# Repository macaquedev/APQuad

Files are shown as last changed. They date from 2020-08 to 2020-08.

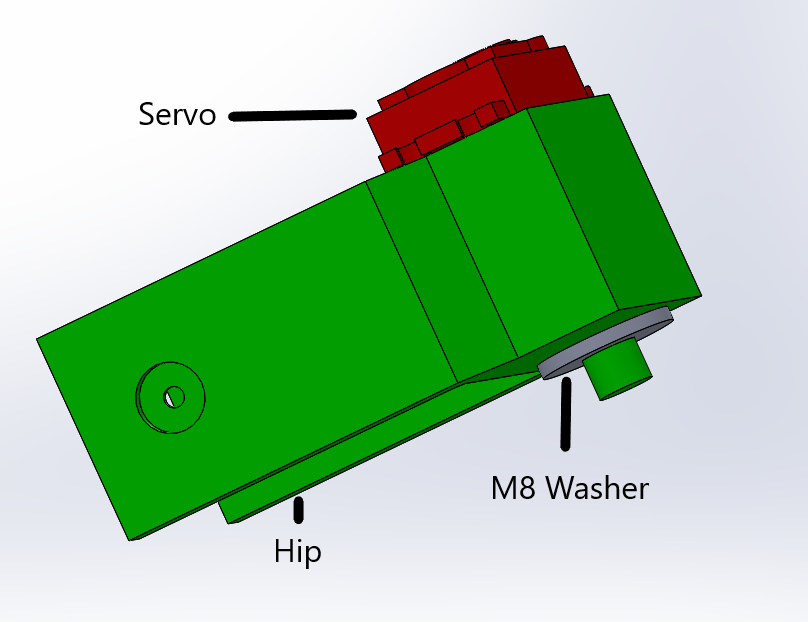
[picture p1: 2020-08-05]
Diymore MG996R/Building Instructions/Photos/Hip Assembly.png

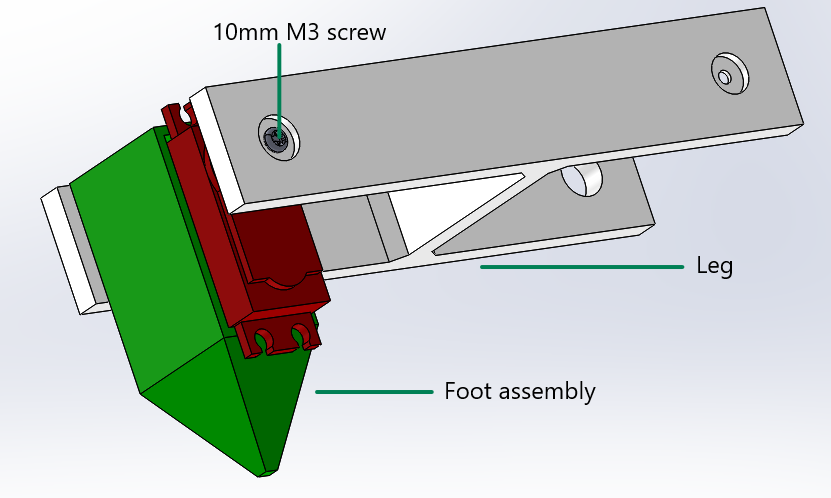
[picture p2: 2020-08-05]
Diymore MG996R/Building Instructions/Photos/Connecting Foot assembly to Leg.png

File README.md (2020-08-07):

An Arduino Quadruped designed to be as straightforward as possible to use and make.

I have posted all code, all STL's and all building instructions on this Github repository.

Please share this repository if you have found this helpful.

Please post a comment or email me at macaquedev@gmail.com if you need help or feel something is wrong.

DISCLAIMER - I hold no responsibility for any damage caused. This is a project that has gone through hours of rigorous testing, which means there is very little risk of something being wrong in the project, but it is very easy to connect something incorrectly. Please double check ALL electronics before switching on your APQuad for the first time.

To start, please clone this repository and then choose a servo out of the ones I have mentioned above. Then please go into the folder with the same name as the servo you are using for your APQuad and read the relevant README files.

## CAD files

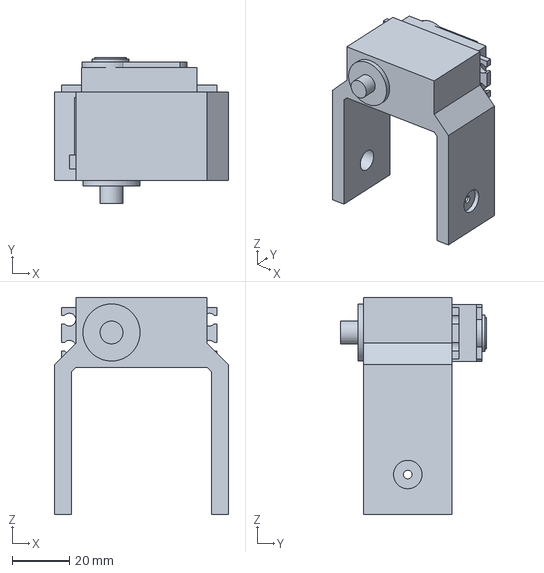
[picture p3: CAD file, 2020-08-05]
Diymore MG996R/Building Instructions/3D Models/Mirrored Hip Assembly.3MF
61.0 x 51.0 x 76.0 mm

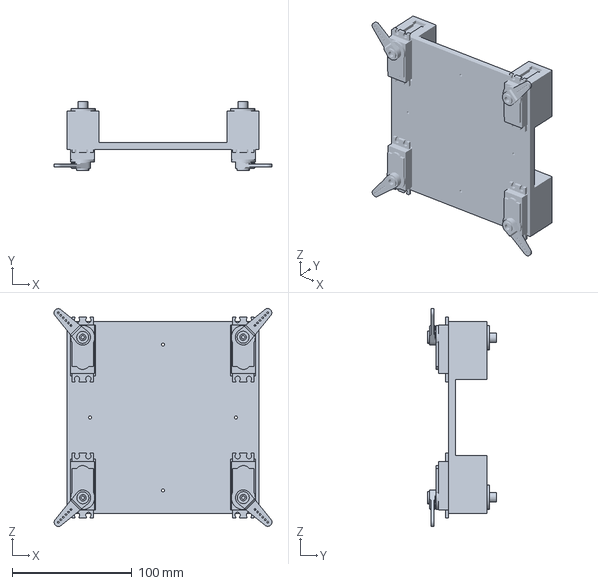
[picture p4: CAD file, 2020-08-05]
Diymore MG996R/Building Instructions/3D Models/Base Plate Assembly.3MF
181.9 x 57.5 x 181.9 mm

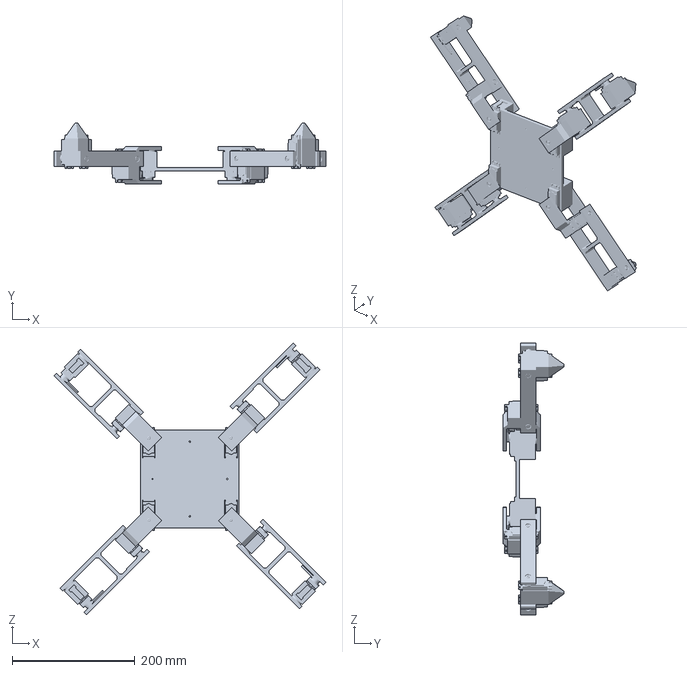
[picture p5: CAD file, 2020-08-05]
Diymore MG996R/Building Instructions/3D Models/Full APQuad Assembly.3MF
442.4 x 99.5 x 441.7 mm

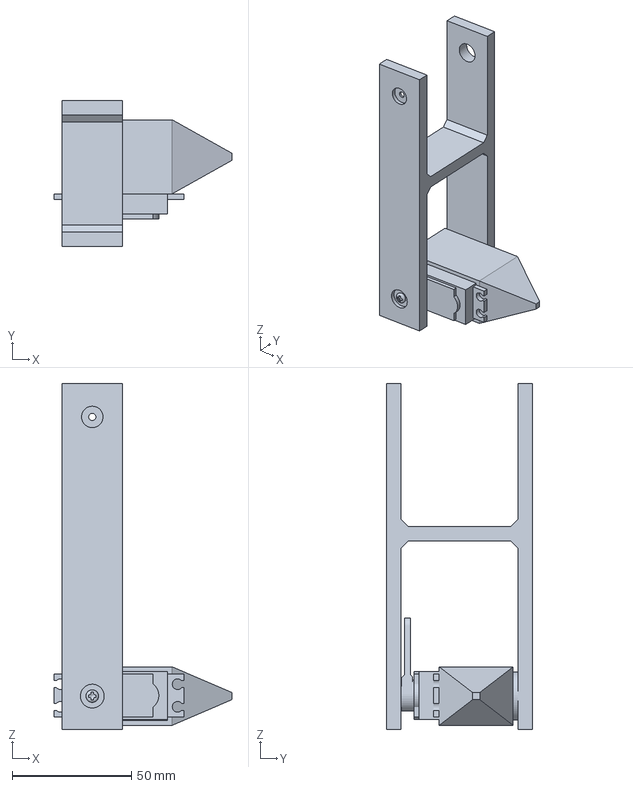
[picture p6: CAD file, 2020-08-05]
Diymore MG996R/Building Instructions/3D Models/Connecting Foot assembly to Leg.3MF
74.5 x 61.0 x 145.0 mm

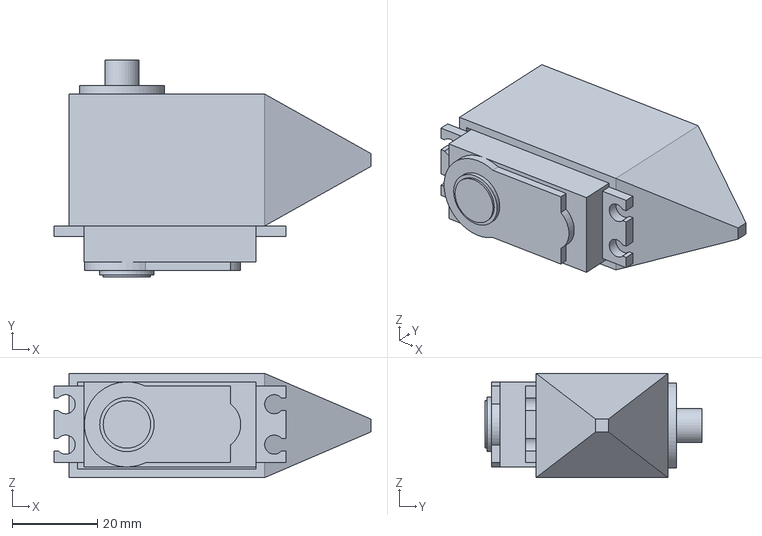
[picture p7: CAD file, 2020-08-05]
Diymore MG996R/Building Instructions/3D Models/Foot assembly.3MF
74.5 x 51.0 x 24.5 mm

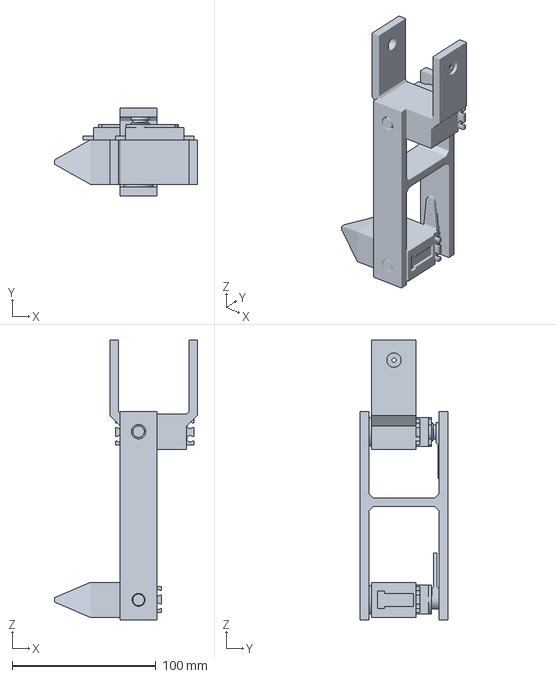
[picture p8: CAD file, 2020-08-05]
Diymore MG996R/Building Instructions/3D Models/Leg with Mirrored Hip assembly.3MF
99.5 x 61.0 x 194.8 mm

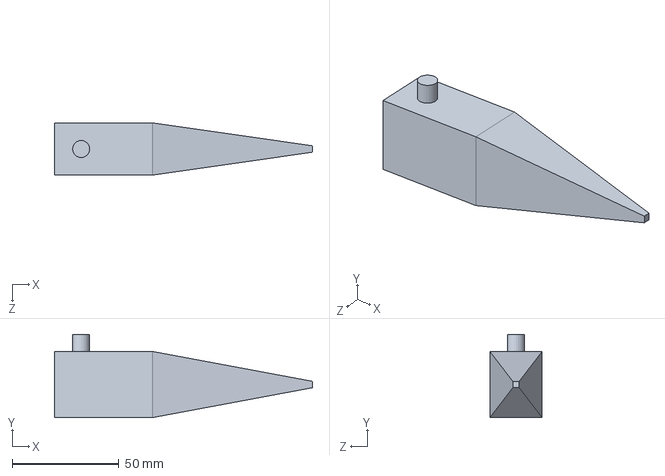
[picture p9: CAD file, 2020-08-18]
Diymore MG996R/SLDPRT (to modify files in Solidworks)/Foot.SLDPRT
121.0 x 39.0 x 24.5 mm

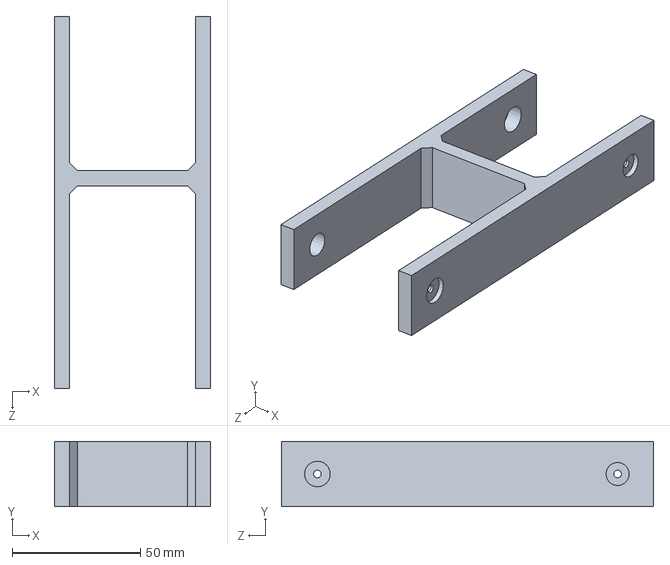
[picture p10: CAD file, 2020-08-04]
Diymore MG996R/SLDPRT (to modify files in Solidworks)/Leg.SLDPRT
61.0 x 25.5 x 145.0 mm

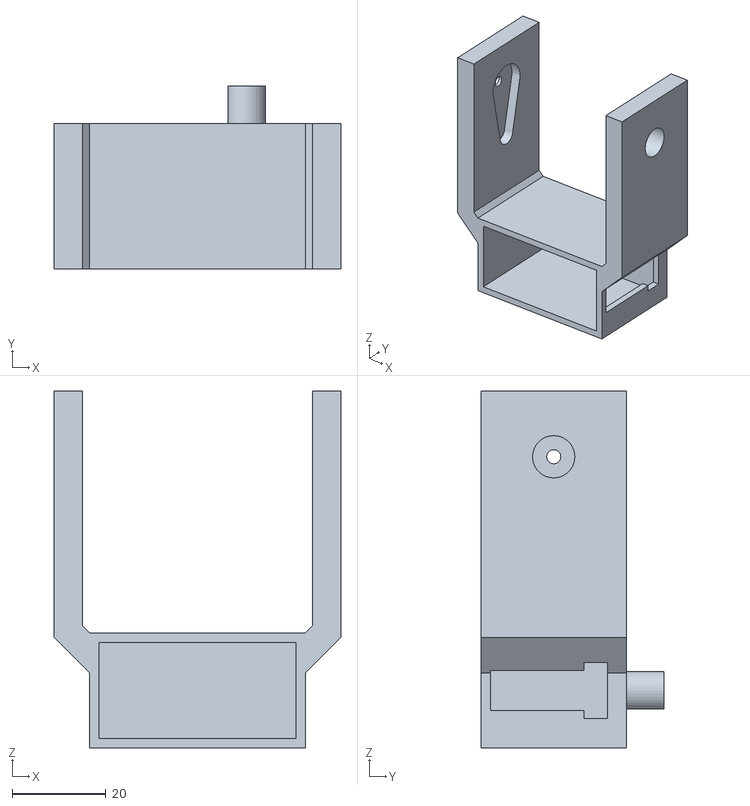
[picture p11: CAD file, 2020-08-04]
Diymore MG996R/To 3D print/Hip.STL
61.0 x 39.0 x 76.0

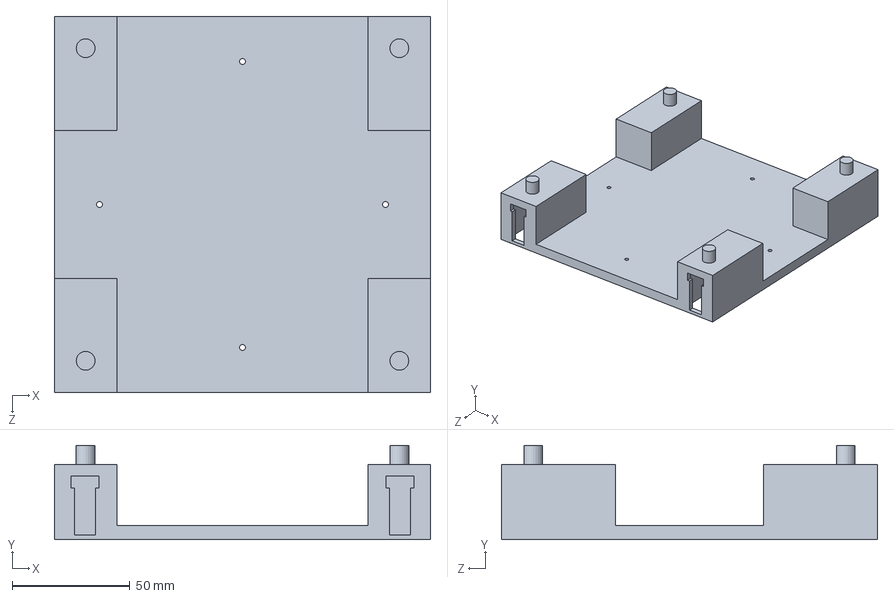
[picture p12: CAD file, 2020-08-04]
Diymore MG996R/SLDPRT (to modify files in Solidworks)/Base Plate.SLDPRT
160.0 x 40.0 x 160.0 mm

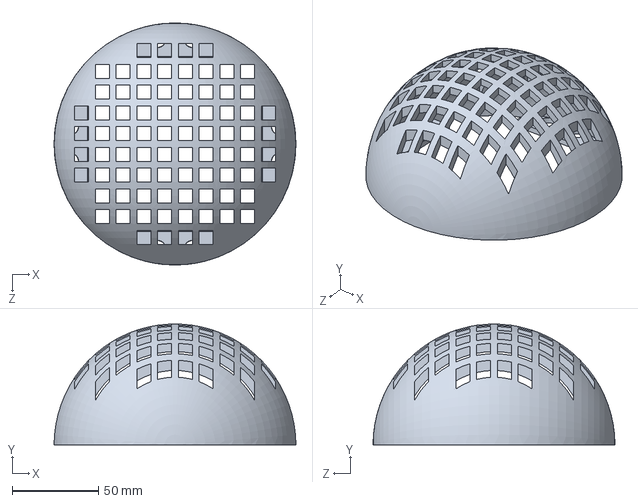
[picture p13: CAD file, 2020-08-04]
Diymore MG996R/SLDPRT (to modify files in Solidworks)/Dome.SLDPRT
140.0 x 69.9 x 140.0 mm

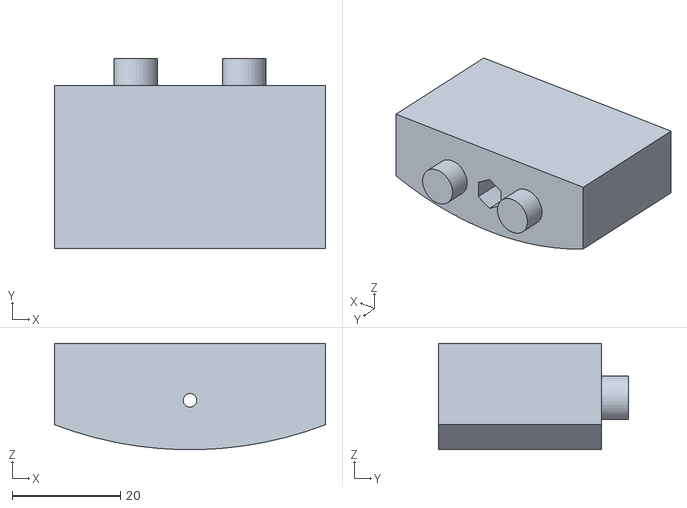
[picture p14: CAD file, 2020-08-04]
Diymore MG996R/To 3D print/Mount for dome.STL
50.0 x 35.0 x 19.6

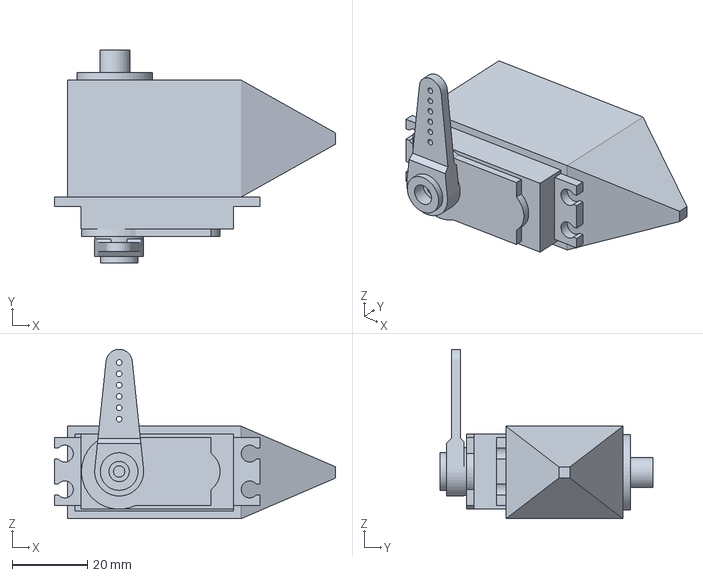
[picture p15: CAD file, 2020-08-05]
Diymore MG996R/Building Instructions/3D Models/Adding attachment to Foot.3MF
74.5 x 56.5 x 44.9 mm

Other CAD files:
Diymore MG996R/Building Instructions/3D Models/Hip Assembly.3MF
Diymore MG996R/Building Instructions/3D Models/Leg with Hip assembly.3MF
Diymore MG996R/To 3D print/Foot.STL
Diymore MG996R/To 3D print/Leg.STL
Diymore MG996R/SLDPRT (to modify files in Solidworks)/Hip.SLDPRT
Diymore MG996R/Building Instructions/3D Models/Adding attachment to Hip.3MF
Diymore MG996R/Building Instructions/3D Models/Adding attachment to Mirrored Hip.3MF
Diymore MG996R/SLDPRT (to modify files in Solidworks)/Leg with tabs for warping prevention.SLDPRT
Diymore MG996R/SLDPRT (to modify files in Solidworks)/Mirrored Hip.SLDPRT
Diymore MG996R/SLDPRT (to modify files in Solidworks)/Mount for dome.SLDPRT
Diymore MG996R/To 3D print/Base Plate.STL
Diymore MG996R/To 3D print/Dome.STL
Diymore MG996R/To 3D print/Leg with tabs for warping prevention.STL
Diymore MG996R/To 3D print/Mirrored Hip.STL

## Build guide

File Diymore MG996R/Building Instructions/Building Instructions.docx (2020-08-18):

Building Instructions for APQuad 3DoF models

Alex Pylypenko (macaquedev)

NOTE:

These will work for ANY model of APQuad with ANY servo (other than 2DOF versions). The parts may look slightly different depending on which model you have, but please rest assured that the assembly WILL be correct no matter which servo is used. However, the Electronics part is slightly different for 9g servos.

DISCLAIMERS:

I hold NO responsibility whatsoever for any damage done or injuries caused by carelessness or incorrect assembly.

This is presented ‘as is’ with ABSOLUTELY NO WARRANTY.

Mechanical Assembly:

3D printed parts required (can be commercially printed):

1x Base Plate.stl

4x Foot.stl

4x Leg.stl

2x Hip.stl

2x Mirrored Hip.stl

These files are located in the ‘To 3D print folder’

Optional:

1x Dome.stl

3x Mount for dome.stl

Mechanical parts required:

12x Servo motors (please use the servo you chose the designs for)

12x M8 washers

15x 10mm M3 screws (12 if not using dome)

Tools required:

Screwdriver (type dependent on the screws you are using)

3D printer

Prusaslicer or equivalent slicer (unless printed commercially)

Note before assembly: if any of this is unclear, please go into:

Building Instructions/3D Models and then see 3D models.

Instructions:

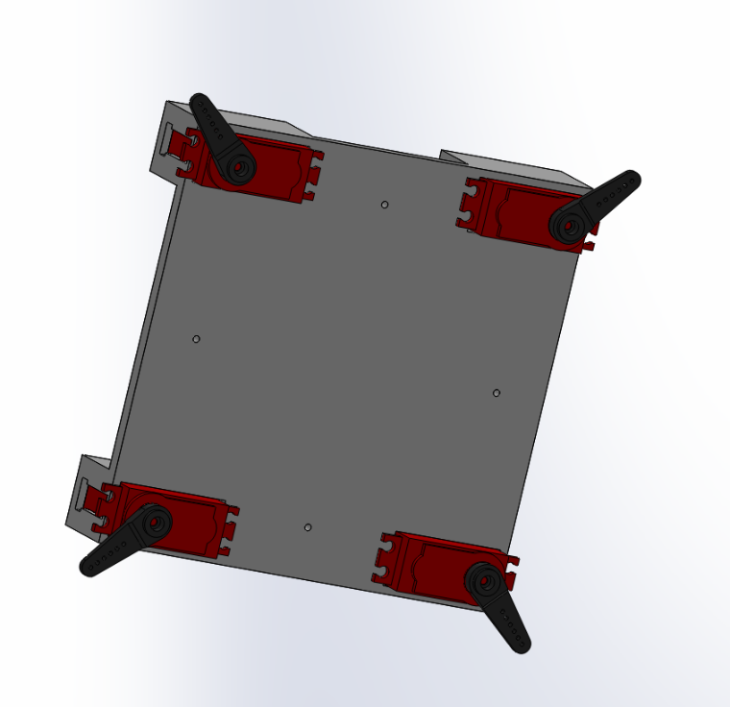
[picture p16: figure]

1. Assemble the base plate as per the images below

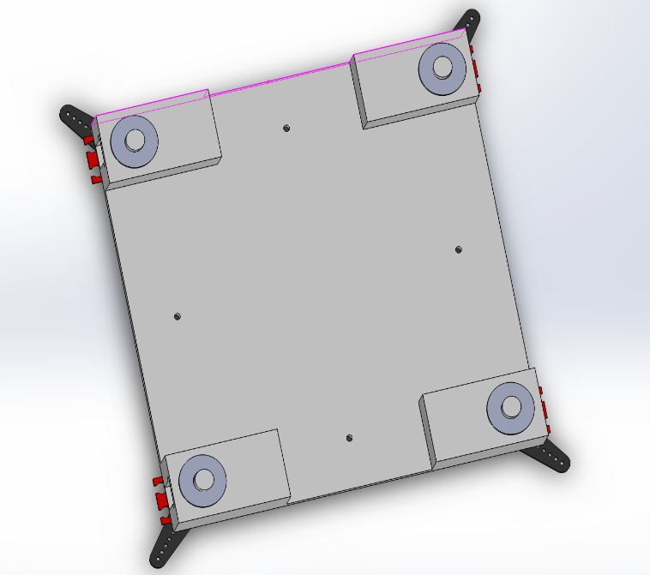
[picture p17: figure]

This step requires 4 servos, 4 washers, 4 attachments and a Base Plate.

This step is rather self-explanatory. However, before attaching the servo attachments completely, please attach them so that the angles shown on the image are the midpoints of the servo’s full turn angle so that the Arduino command moveServo(blh, 90); moves the back left hip to the position illustrated in the diagram above (top left).

2. Assemble all the feet as per the image below.

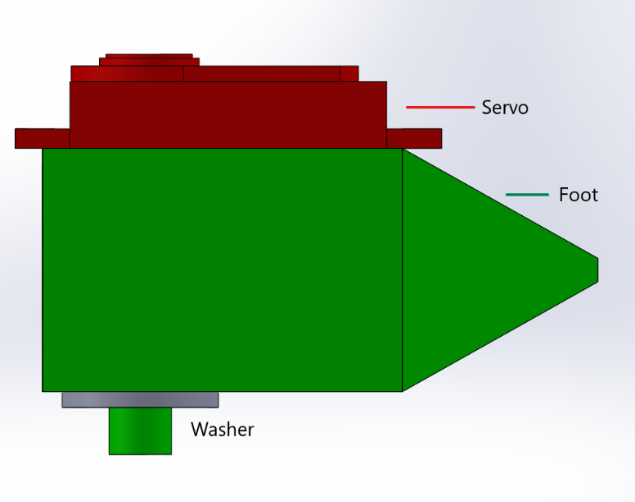
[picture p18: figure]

3. Add the attachments onto the servos. Please follow the instructions in step 1 as to what to do with the attachments (regarding midpoints etc.), however, please make 2 feet as in the diagram below and 2 feet with the attachment 180 degrees from where it is in the diagram below. Please keep the ones that are as per the diagram away from the mirrored ones and please remember which ones aren’t mirrored and which ones are.

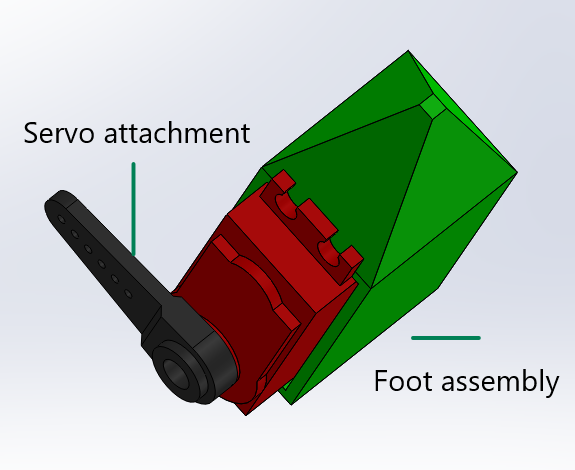
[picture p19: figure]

4. Add the legs to the foot assemblies. The mirrored ones and the non-mirrored ones will look slightly different, but that is totally correct.

Please make sure that the servo attachment goes into its designated hole. Please put it into the LONGER end of the leg.


5. Assemble the two hips and the two mirrored hips as shown in the diagrams below. Again, the angles shown in the diagram should be the midpoint of the servo’s angle of rotation.

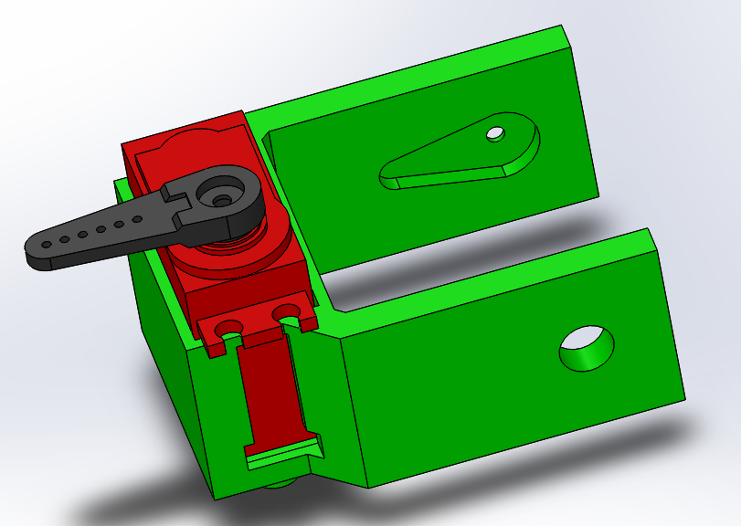
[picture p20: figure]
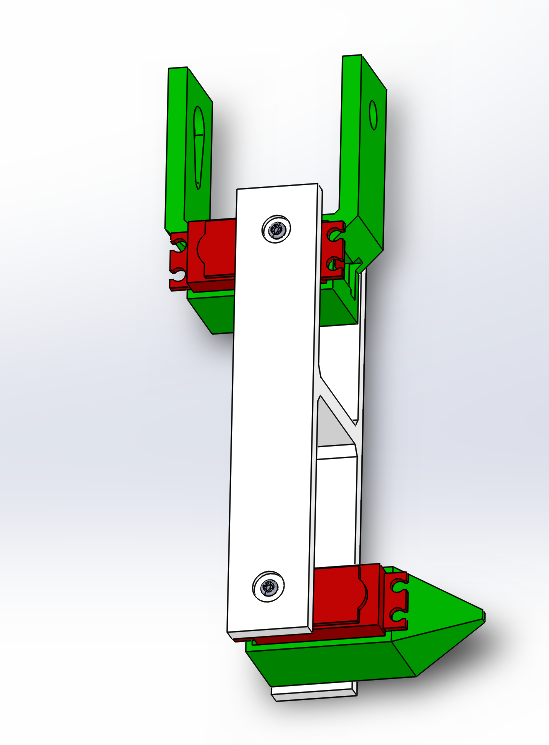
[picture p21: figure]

6. Insert the hips into the non-mirrored legs and the mirrored hips into the mirrored legs into the other ends of the leg. Please see diagram on how this should look. If it doesn’t look right, you have probably used a non-mirrored leg with a mirrored hip.
7. Before finishing the mechanical assembly of the APQuad, make sure that you have the following:
  a. 2 Legs with normal Hips
  b. 2 Legs with Mirrored Hips
  c. A fully assembled Base Plate as shown in Step 1

If not, please reread the manual. As an ABSOLUTE LAST RESORT, please email macaquedev@gmail.com with DETAILED information about your issue. Please include photos if possible. I will be very happy to answer any questions but please consider the fact that I am very busy. I will try to respond to any emails within 24 hours but if this isn’t the case, please do not spam me with emails.

8. If you have completed the checklist in question 7, please finish assembling your APQuad as shown below. The front of the APQuad is on between the top 2 legs on the image.

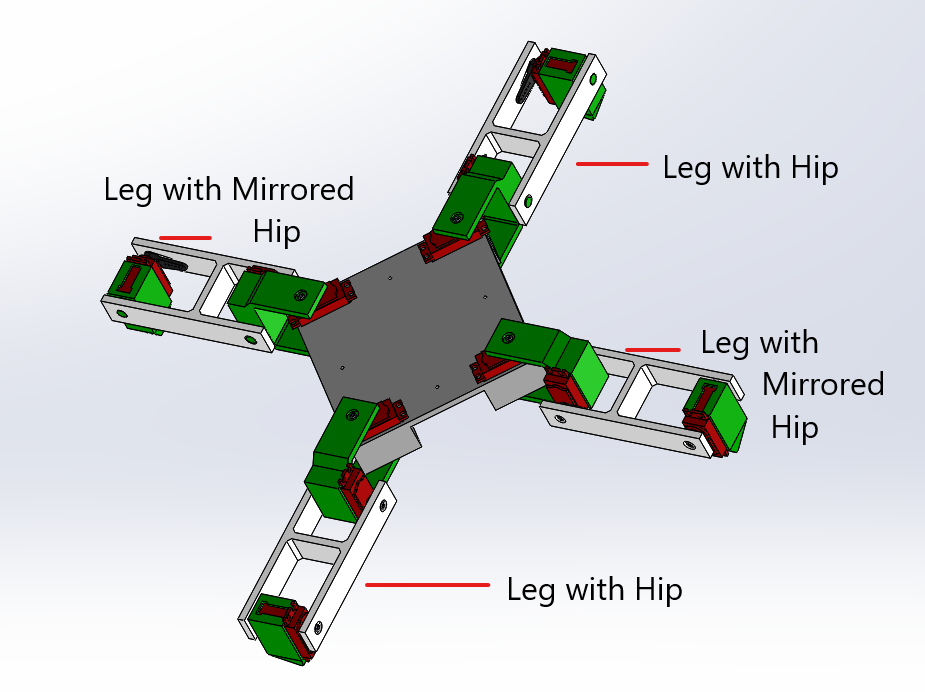
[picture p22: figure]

This is the end of the mechanical assembly. Please carry on with the electronic assembly.

Electronics Assembly (for non-9g servos):

Parts required:

Arduino Nano

PCA9685 servo multiplexer

A 3s LiPo battery

A load of jumper wires of all types

Thick wire (for high amperages)

Thinner wire (for low amperages)

R1966ablkblkff switch

10A 150W DC DC stepdown converter

LM2596S stepdown converter

A piece of PCB

Tools required:

Glue Gun

Soldering iron

Multimeter

NOTE: THIS PART IS QUITE FIDDLY AND IT IS VERY EASY TO DO SOMETHING WRONG. LITHIUM BATTERIES ARE VERY FLAMMABLE AND CAN CAUSE A MAJOR FIRE IF NOT CONNECTED PROPERLY.

Connect both converters in parallel to the battery through the switch. Check that output voltage of both converters is exactly 5V when supplying battery’s output voltage. Connect the Arduino to the 2A converter via VIN and the servo board to the 10A converter via the terminal block.

Solder 3 rows of roughly 10 female pin headers. Connect them together underneath using a soldering iron. Connect 1 row to Ground, 1 row to 3.3v and 1 row to 5v

Electronic Assembly for 9g servos:

Parts required:

Arduino Nano (use a clone to save money)

PCA9685 servo multiplexer

A 2s LiPo battery (I salvaged one from an old laptop but any will do)

A load of jumper wires of all types

Thick wire (for high amperages)

Thinner wire (for low amperages)

R1966ablkblkff switch

2x LM2596S stepdown converter

A piece of PCB

Tools required:

Glue Gun

Soldering iron

Multimeter

NOTE: THIS PART IS QUITE FIDDLY AND IT IS VERY EASY TO DO SOMETHING WRONG. LITHIUM BATTERIES ARE VERY FLAMMABLE AND CAN CAUSE A MAJOR FIRE IF NOT CONNECTED PROPERLY.

Connect both converters in parallel to the battery through the switch. Check that output voltage of both converters is exactly 5v when supplying battery’s output voltage. Connect the two converters’ outputs together. Connect both the Arduino (via VIN) and the servo board (via terminal holes) to the converters’ outputs.

Solder 3 rows of roughly 10 female pin headers. Connect them together underneath using a soldering iron. Connect 1 row to Ground, 1 row to 3.3v and 1 row to 5v

Electronic Assembly continued for ALL servos:

Connect the servo board to the Arduino:

Servo Board | Arduino (or power rail if applicable)
GND | GND
VCC | 3.3v
SCL | A5
SDA | A4

Connect the servos to the Servo Board:

B=back, F=front, L=left, R=right, A=ankle, K=knee, H=hip

Servo | Servo
FLA | 0
FLK | 1
FLH | 2
FRA | 3
FRK | 4
FRH | 5
BLA | 6
BLK | 7
BLH | 8
BRA | 9
BRK | 10
BRH | 11

This is it for the Electronic Assembly.

NOTE: It is recommended for the Arduino Nano’s USB to be facing the back of the robot and to be easy to access from outside.

Adding the Dome (optional):

This step is extremely self-explanatory. Note – the part missing a Mount should be where the Arduino Nano’s USB port is facing. This is done so that the USB port is easily accessible.

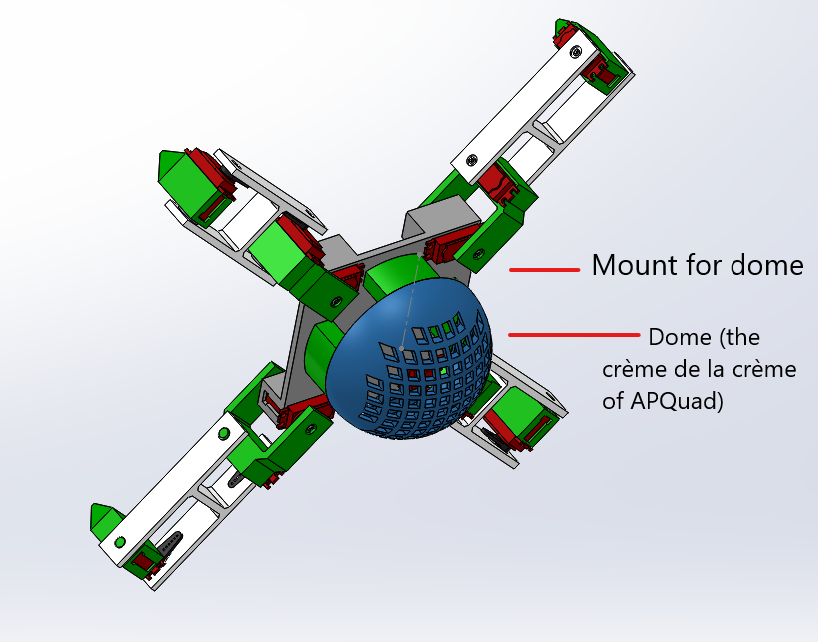
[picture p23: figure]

Uploading the Firmware:

Please install the latest version of the Arduino IDE (do not use the web editor).

Go to Sketch → Include Library → Add .ZIP library and then browse for APQuad.zip.

Then, when you need to use APQuad commands, use the ones below.

Also, examples are provided. Go to File → Examples and then scroll down to custom libraries. You should see APQuad. Go to demo. It is a good representation of what your APQuad can do. The possibilities are endless!

It is really that simple!

For more experienced devs: I challenge you to create another APQuad function and send it to me so I can include it in the APQuad.h file with your name attributed to it!

Criteria:

1. To move a servo, please use my moveServo function
2. Please look at the APQuad.h file in the library and see how it is laid out.
3. Please don’t pass more than 4 arguments to a function – it simply overcomplicates the design.
4. Please don’t litter the global namespace using #defines or global variables!
5. NOTE: THIS IS NOT REQUIRED: If possible, please send me a video to macaquedev@gmail.com of your APQuad doing that manoeuvre.

Commands that you can use to move the APQuad are on the next page:

APQuad q(ServoType, I2C_ADDRESS); // replace q with anything you want to call your APQuad object. For ServoType, use the namespace ServoTypes with the servo you are using. For example, ServoTypes::MG996R or ServoTypes::SG90. I2C_ADDRESS is the I2C_ADDRESS of your board. Please leave blank if unsure as it will default to 0x40 and work 99 percent of the time. Please just use “APQuad q;” if you are using SG90 servos want to be safe. For the rest of the commands, replace the initial q with your APQuad object’s name. Or just stick with q in the whole program to make life easier!

q.initializeQuad(); // This is mandatory in void setup() otherwise the quad won’t walk.

q.unfold(speed_lower_is_faster); // Unfolds the robot, folded() returns false

q.fold(speed_lower_is_faster); // Folds the robot, folded() returns true

q.folded(); // returns true at beginning of program as it assumes that the robot was folded while turned off. returns

q.stepForwardsCreepGait(steps, speed_lower_is_faster);

q.stepBackwardsCreepGait(steps, speed_lower_is_faster);

q.stepLeftCreepGait(steps, speed_lower_is_faster);

q.stepRightCreepGait(steps, speed_lower_is_faster);

q.stepForwardsTrotGait(steps, speed_lower_is_faster);

q.stepBackwardsTrotGait(steps, speed_lower_is_faster);

q.stepLeftTrotGait(steps, speed_lower_is_faster);

q.stepRightTrotGait(steps, speed_lower_is_faster);

q.turnRight(steps, speed_lower_is_faster);

q.turnLeft(steps, speed_lower_is_faster);

q.raiseBody(degrees, speed_lower_is_faster); // negative degrees lower body

q.pressUp(x); // Does x press-ups

q.squat(x); // Does x squats

q.moveServo(servo, pos); moves servo to position pos.

Servo can be from 0 to 15 on the PCA9685 board.

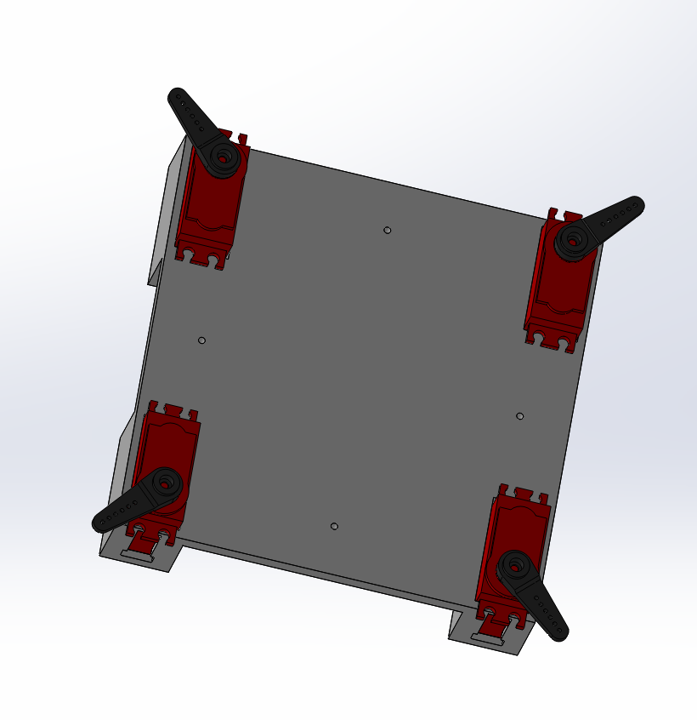
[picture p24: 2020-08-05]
Diymore MG996R/Building Instructions/Photos/Base Plate assembly 1.png

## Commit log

2020-08-05 Added Building Instructions
    [Adding attachment to Foot.3MF, Adding attachment to Hip.3MF, Adding attachment to Mirrored Hip.3MF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]
2020-08-18 Updated firmware to not litter global namespace
    [Foot.SLDPRT, Foot.STL]
